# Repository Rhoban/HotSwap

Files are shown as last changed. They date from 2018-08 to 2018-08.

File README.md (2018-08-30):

# Hot swap

This is a simple hot swap board for dynamixel

## Features

With this system, when a battery is plugged, the LOGIC (for instance the robot computer) is powered through a diode, allowing a second battery to be plugged simultaneously

The SPDT switch allow to choose which battery is powering the motors, allowing an hot swap of the battery with the following sequence:

* Plugging the second battery
* Switching the SPDT switch
* Unplugging the first battery

The robot's computer will not reboot and the motors are now powered by the new battery

## 3 buses wiring

This Dynamixel HUB features 8 connectors, which have the same power supply but separated buses, with purpose to be combined with triple buses [Rhoban DXLBoard](http://github.com/Rhoban/DXLBoard):

* 2 connectors for leg 1
    * One should be connected to the first bus of the DXLBoard
    * The other should be connected to the first motor of one leg (the other are daisy chained)
* 4 connectors for the torso
    * One is connected to the second bus of the DXLBoard
    * The second to the first motor of left shoulder
    * The third to the first motor of right shoulder
    * The last to the first motor of the head
* 2 connectors for leg 2
    * One is connected to the second bus of DXLBoard
    * The other is connected to the other leg first mother

Then, the motors should be dispatched on three separate bus, one for left leg, one for right leg and one for the upper body of the robot.

## Components

You can find all the required components in the ``BOM.xlsx`` file. Note that you should choose between 3 and 4 pins for your dynamixel connectors.

* Switch
    * https://fr.farnell.com/arcolectric/c1520ataaa/interrupteur-a-bascule-spdt-ctr/dp/150551
    * Farnell ref: 150551
    * Constructor ref: C1520ATAAA 
* Double diode
    * https://fr.farnell.com/on-semiconductor/mbr1545ctg/diode-schottky-15a-45v-to-220/dp/1431049
    * Farnell ref: 1431049
    * Constructor ref: MBR1545CTG
* Dynamixel MOLEX connectors
    * 3 pins: https://fr.farnell.com/molex/22-03-5035/embase-droite-2-5mm-3-voies/dp/9979620
    * Farnell ref: 9979620
    * Constructor ref: 22-03-5035 
    * 4 pins: https://fr.farnell.com/molex/22035045/embase-vertical-2-5mm-4-voies/dp/1104204
    * Farnell ref: 1104204
    * Constructor ref: 22035045

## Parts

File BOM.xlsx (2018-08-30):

 |  |  | Rhoban HotSwap Board Bill of materials
Item # | *Ref Des | *Qty | Manufacturer | *Mfg Part # | Description / Value | *Package | Type | Your Instructions / Notes
1 | DXL1, DXL2, DXL3, DXL4, DXL5, DXL6, DXL7, DXL8 | 8 | MOLEX | 22-03-5035 (3 PIN) OR 22-03-5045 (4 PIN) | Connector | - | Thru-Hole | Farnell : 9979620 OR 1104204
2 | U$1 | 1 | ON SEMICONDUCTOR | MBR1545CTG | Double Diode | TO-220 | Thru-Hole | Farnell : 1431049
3 | U$2 | 1 | ARCOELECTRIC | C1520ATAAA | SPDT Switch | - | Thru-Hole | Farnell : 150551
Click for Instructions on How to Create a BOM (https://www.pcbway.com/blog/PCB_Assembly/How_to_Build_a_BOM__Bill_Of_Materials_.html)

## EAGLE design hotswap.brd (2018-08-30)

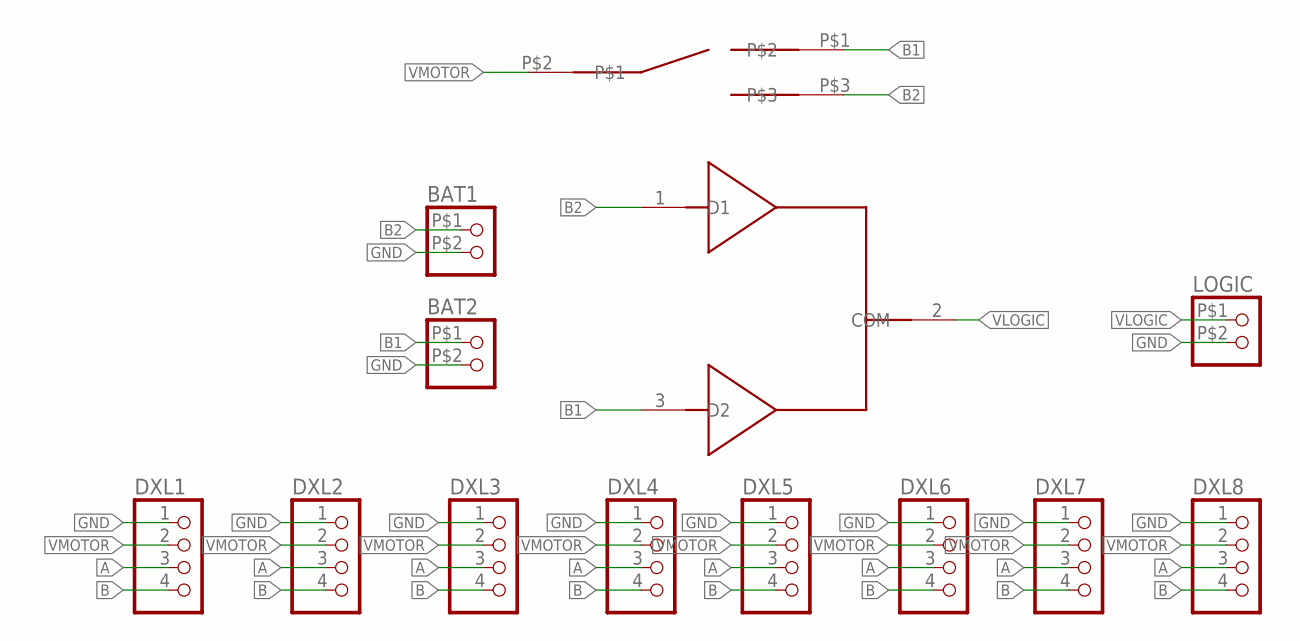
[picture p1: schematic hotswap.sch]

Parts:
BAT1, BAT2: CONNEC_1X02BIG; CONNEC_1X02_BIG
DXL1, DXL2, DXL3, DXL4, DXL5, DXL6, DXL7, DXL8: CONNEC_1X04; FARNELL 9979620 OR 1104204
LOGIC: CONNEC_1X02BIG; CONNEC_1X02_BIG
U$1: MBR1545CTG; TO-220-ALT; FARNELL 1431049
U$2: BIG_SPDT; FARNELL 150551

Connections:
A: DXL1.3, DXL2.3, DXL3.3, DXL4.3, DXL5.3, DXL6.3, DXL7.3, DXL8.3
B: DXL1.4, DXL2.4, DXL3.4, DXL4.4, DXL5.4, DXL6.4, DXL7.4, DXL8.4
B1: BAT2.P$1 (1), U$1.3 (D2), U$2.P$1
B2: BAT1.P$1 (1), U$1.1 (D1), U$2.P$3
GND: BAT1.P$2 (2), BAT2.P$2 (2), DXL1.1, DXL2.1, DXL3.1, DXL4.1, DXL5.1, DXL6.1, DXL7.1, DXL8.1, LOGIC.P$2 (2)
VLOGIC: LOGIC.P$1 (1), U$1.2 (COM)
VMOTOR: DXL1.2, DXL2.2, DXL3.2, DXL4.2, DXL5.2, DXL6.2, DXL7.2, DXL8.2, U$2.P$2

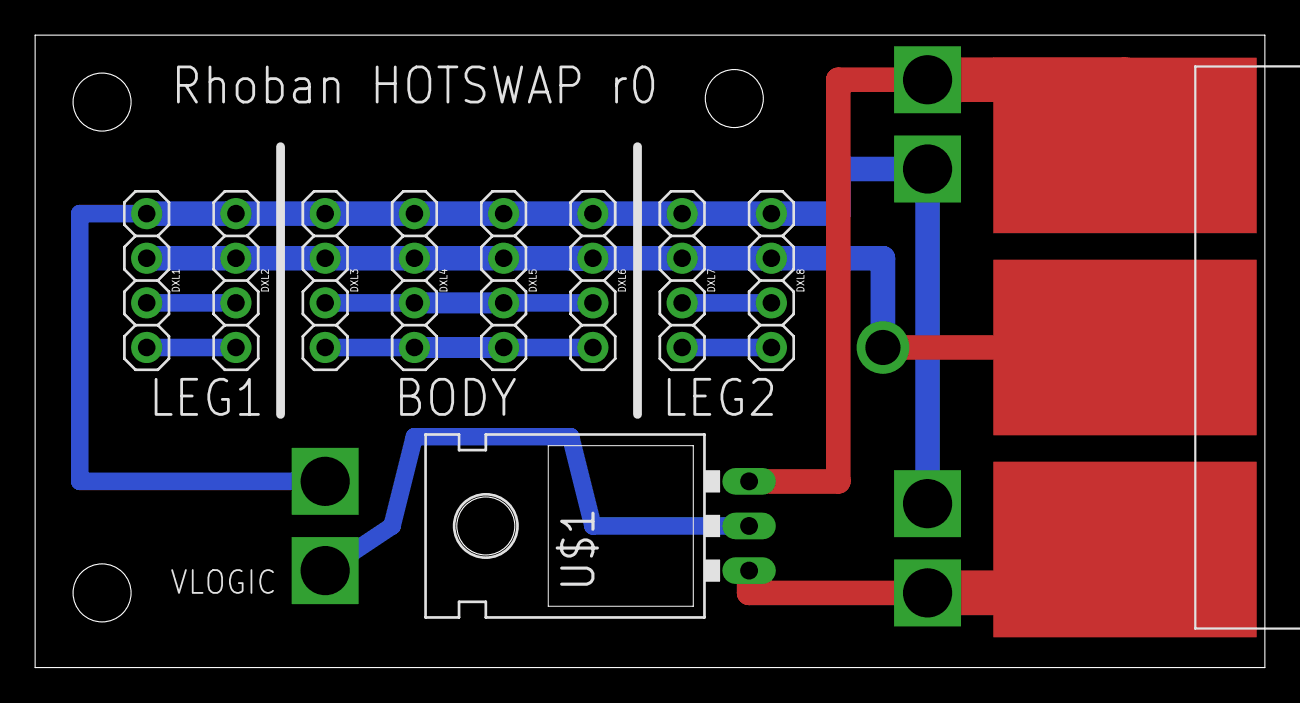
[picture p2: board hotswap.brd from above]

Board: 2 copper layers, 70.0 x 36.0 mm, 16 parts (0 on the bottom side), 7 nets.

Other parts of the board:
U$3, U$4, U$5: STAND-OFF

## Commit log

2018-08-10 Hot swap
    [hotswap.brd, hotswap.sch]
2018-08-30 Fixing FARNELL attributes and writing BOM
    [BOM.xlsx, hotswap.brd, hotswap.sch]
2018-08-30 Fixing item #
    [BOM.xlsx]

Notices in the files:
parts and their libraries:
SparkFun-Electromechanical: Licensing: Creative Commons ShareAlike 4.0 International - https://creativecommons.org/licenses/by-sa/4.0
